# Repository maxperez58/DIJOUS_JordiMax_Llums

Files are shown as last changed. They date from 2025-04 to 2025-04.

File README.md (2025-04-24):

View this project on [CADLAB.io](https://cadlab.io/project/28977). 

DIJOUS_JordiMax_Llums

## Autors
- Max Pérez (@maxperez58)
- Jordi Godàs (@Jordi_Godas)

## Versió - v1.0 ## Curs - Assignatura de Disseny de PCBs amb KiCad - [Curs 2024-2025]

## Objectiu Descripció breu de l'objectiu del projecte.

L'objectiu d'aquest projecte és la realització d'un sistema de control per els diferents tipus de llums d'un vehícle automòvil. A més a més, s'ha incorporat un motor per al control de l'escombreta neteja-fars.

## Requisits i especificacions
- Llums curtes.
- Llums d'encreuament.
- Llums de circulacio dïurna.
- Intermitents.
- Motor escombreta neteja-fars.
- Sensor digital de llum, per activar les llums.

## Diagrama de blocs (Afegiu una imatge del diagrama de blocs)
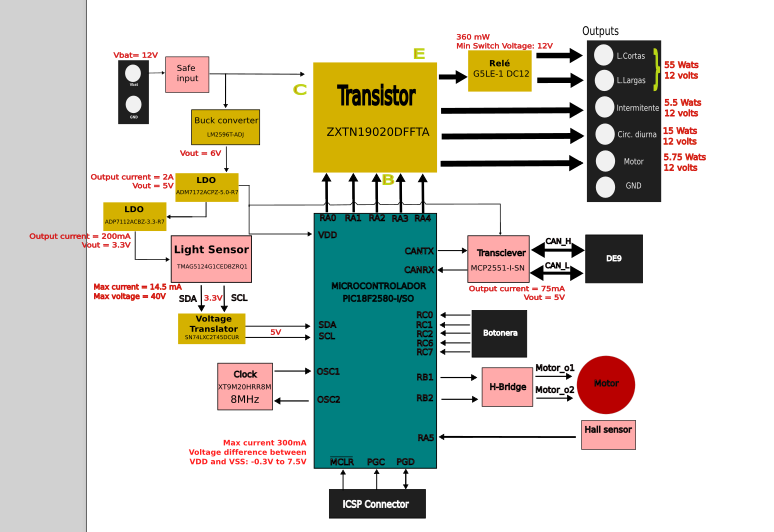
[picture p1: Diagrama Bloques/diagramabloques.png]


_Figura 1.1: Diagrama de Blocs del nostre projecte_

## Taula de components
| Descripció | Manufacturer Number | Package | Datasheet | Proveïdor | Unitats |
|---|---|---|---|---|---|
| LDO-5V | REG1117-5 |SMD| [LT1117-5](https://www.mouser.es/datasheet/2/609/1117fd-2953685.pdf)| Mouser | 1 |
| LDO-3.3V | ADP7112ACBZ-3.3-R7 |SMD| [ADP7112ACBZ-3.3-R7 ](https://www.mouser.es/datasheet/2/609/ADP7112-3121706.pdf)| Mouser | 1 |
| Sensor de llum | BH1750FVI-TR |SMD| [BH1750FVI-TR](https://www.mouser.com/catalog/specsheets/Rohm_11162017_ROHMS34826-1.pdf)| Mouser | 1 |
| Relé | G5LE-1 DC12 |TO-220| [G5LE-1 DC12](https://www.mouser.es/datasheet/2/307/en_g5le-3447037.pdf)| Mouser | 2 |
| Buck converter | LM2596T-ADJ |SMD| [LM2596T-ADJ](https://www.ti.com/lit/ds/symlink/lm2596.pdf)| Texas Instruments | 1 |
| Transciever| MCP2551-I-SN |SMD| [MCP2551-I-SN](https://ww1.microchip.com/downloads/en/devicedoc/21667d.pdf) | Texas Instruments | 1 |
| Microcontrolador | PIC18F2580-I/SO |SMD| [PIC18F2580-I/SO](https://www.mouser.es/datasheet/2/268/39637d-3443674.pdf) | Mouser | 1 |
| Transistor NMOS | Si7336ADP |SMD| [Si7336ADP](https://www.vishay.com/docs/73152/si7336adp.pdf)| Mouser | 4 |
| Transistor BJT | ZXTN19020DFFTA |SMD| [ZXTN19020DFFTA](https://www.diodes.com/assets/Datasheets/ZXTN19020DFF.pdf) | Mouser | 5 |
| Traductor (3.3V-5V) | PCA9306D |SMD|[PCA9306D](https://www.ti.com/lit/ds/symlink/pca9306.pdf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) | Mouser | 1 |
| Sensor hall | TMAG5124G1CEDBZRQ1 |SMD| [TMAG5124G1CEDBZRQ1](https://www.ti.com/lit/ds/symlink/tmag5124-q1.pdf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) | Mouser | 1 |
| OPAMP's | LT6202CS5 |SMD| [LT6202CS5](https://www.mouser.es/datasheet/2/609/620234fd-2955338.pdf) | Mouser | 1 |
| Voltage Regulator | TLV1117-33 |SMD| [TLV1117-33](http://www.ti.com/lit/ds/symlink/tlv1117.pdf) | Mouser | 1 |
| Cristall | XT9M20ANA8M |SMD| [XT9M20ANA8M](https://datasheet.octopart.com/XT9M20ANA8M-Vishay-datasheet-41303490.pdf) | Mouser | 1 |
| Inductance | Ms 42 / 47 µH |SMD| [Ms 42 / 47 µH](https://neosid.de/import-data/product-pdf/neoFestind_Ms42.pdf) | Mouser | 1 |
| Diode | 1N4002 |THT| [1N4002](https://diotec.com/request/datasheet/1n4001.pdf) | Mouser | 1 |
| Diode | 1N5817 |THT| [1N5817](http://www.vishay.com/docs/88525/1n5817.pdf) | Mouser | 4 |
| LED | APTR3216PGW |SMD| [APTR3216PGW](https://www.mouser.es/datasheet/2/216/kingbright_kngbd00006-5-1736195.pdf) | Mouser | 2 |
| Zener diode | BZX84C39 |SMD| [BZX84C39](https://diotec.com/request/datasheet/bzx84c2v4.pdf) | Mouser | 1 |
| Diode | 1N4148 |THT| [1N4148](https://assets.nexperia.com/documents/data-sheet/1N4148_1N4448.pdf) | Mouser | 1 |
| Diode Schottky | SS3P5HM3/84A |SMD| [SS3P5HM3/84A](https://www.vishay.com/docs/88944/ss3p3.pdf) | Mouser | 1 |

## Funcionalitats de les diverses seccions del nostre circuit
- [ ] Secció 1: secció de Power que converteix els 12 volts de VBAT a 5 volts per +Vcc i els 3.3 volts pel sensor.
- [ ] Secció 2: resistències pull-down a l'input per evitar una entrada descontrolada en cas de no connexió.
- [ ] Secció 3: secció del sensor amb traductor de nivell per garantir la bona comunicació entre sensor i microcontrolador.
- [ ] Secció 4: Etapa d'entrada del sensor Hall, el qual està destinat a comptar les voltes del motor.
- [ ] Secció 5: Etapa de comunicacions basada en un transciever el qual serveix per connectar el micro a un bus CAN.
- [ ] Secció 6: Etapa digital, formada pel micro i els seus I/0 + ICSP + Clock
- [ ] Secció 7: Pont-H + resistència Shunt, que controlen el sentit de gir del motor i detecten possibles pics de tensió
- [ ] Secció 8: etapa de selecció, on segons el corrent de base dels transistors i el voltatge aplicat al relé, s'escull un tipus d'iluminació o un altre.
- [ ] Secció 9: etapa reservada pels outputs i el connector DB-9 del bus CAN

## Historial de canvis 
| Data | Autor | Branch | Descripció |
|---|---|---|---|
| 2025-03-17 | Max Pérez | `main` | Creació del projecte |
| 2025-03-17 | Max Pérez | `main` | LDO y output select stage |
| 2025-03-18 | Max Pérez | `main` | Conexiones básicas micro|
| 2025-03-18 | Max Pérez | `main` |Bloque transceiver, safe input y Clock|
| 2025-03-18 | Max Pérez |  `main` |Mejora estética|
| 2025-03-19 | Jordi Godàs | `main`|Acabar el diagrama de blocs 1.0|
| 2025-03-19 | Jordi Godàs |  `main` |Acabar el power point de la presentació|
| 2025-03-21 | Max Pérez | `main` |Creación esquemático 1.0|
| 2025-03-21 | Max Pérez | `main` |Bloques Clock, Communication, Digital Esquemático 1.0|
| 2025-03-21 | Max Pérez |  `main` |Bloques Input, Sensor, Power Esquemático 1.0|
| 2025-03-22 | Max Pérez |  `main` |Mejora etapa Power cambiando DC/DC + LDO por Buck|
| 2025-03-21 | Max Pérez | `main` |Capacidades desacoplo, comentar esquemático y bloque output|
| 2025-03-24 | Max Pérez |  `main` |Simulación Power stage (1 buck y 2 LDO). Exitosa|
| 2025-03-25 | Max Pérez |  `main` |Simulación Power stage (1 buck y 2 LDO) v2 y simulación Puente H|
| 2025-03-27 | Jordi Godàs |  `main` | Actualizar presentacion |
| 2025-03-27 | Jordi Godàs |  `main` | Actualizar el diagrama de bloques y el esquematico con lo dicho en clase por el profesor |
| 2025-03-29 | Max Pérez |  `main` |simulación Puente H v2|
| 2025-03-31 | Max Pérez |  `main` |Placement algunos componentes, separación planos masa y potencia. Routing Transciever, puente H y algun Input Output|
| 2025-04-02 | Jordi Godàs |  `main` | Acabar el layout de la pcb |
| 2025-04-02 | Jordi Godàs |  `main` | Actualizar presentacion |
| 2025-04-02 | Max Pérez |  `main` |GND de SMD + algun ruteo puntual. DRC sin errores|
| 2025-04-03 | Jordi Godàs |  `main` | Cambio del LDO-3.3V y placement en el esquematico |
| 2025-04-03 | Jordi Godàs |  `main` | Update readme |
| 2025-04-06 | Jordi Godàs |  `main` | Update pcb, bigger paths and better organitzation |
| 2025-04-06 | Jordi Godàs |  `main` | Update schemetatic, minor changes |
| 2025-04-07 | Jordi Godàs |  `main` | Finished layout, ERC passed |
| 2025-04-12 | Max Pérez |  `main` | Update readme: update componentes usados + diagrama bloques i funcionalidades secciones|
| 2025-04-07 | Max Pérez |  `main` | Update Esquemàtic: nombrar nodos + corrección conexión etapa Shut|
| 2025-04-09 | Jordi Godàs |  `main` | Update layout: 2CI ERC passed |
| 2025-04-12 | Max Pérez |  `main` | Cambio LDO a 5V dado a la footprint conflictiva del anterior |
| 2025-04-12 | Max Pérez |  `main` | Revisión y sustitución de footprints mal asignadas, así como reorganización en el layout de la etapa de potencia |
| 2025-04-20 | Max Pérez |  `main` | Matriu de preus per a tirada curta PCBs|
| 2025-04-20 | Max Pérez |  `main` | Generació Gerbers|
| 2025-04-20 | Max Pérez |  `main` | Búsqueda precios JCL PCB y referencias en su catálogo|
| 2025-04-23 | Jordi Godàs |  `main` | Tirada curta dels presupostos |

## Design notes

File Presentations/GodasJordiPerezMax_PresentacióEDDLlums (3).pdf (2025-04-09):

# Projecte EDD-Llums

## Max Pérez Piqué Jordi Godàs Mancha

## Eines de Disseny

2024/2025

# Diagrama de blocs

# De què tracta el projecte?

Disseny del sistema de control d'il·luminació d’un cotxe mitjançant un microcontrolador.

# Requisits del projecte

## Parts clau del diagrama:

- Llums de carretera.
- Llums d'encreuament.
- Llums de circulació diürna.

## - Intermitents

- Motor escombreta neteja-fars.
- Sensor digital de llum, per activar les llums.

# Diagrama de blocs

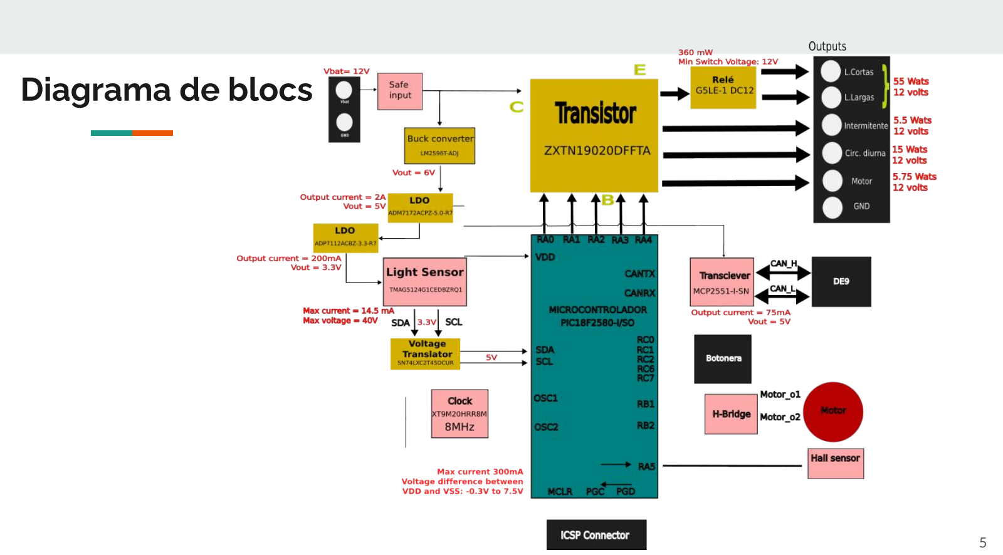
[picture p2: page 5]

# Inputs

# Output selection stage

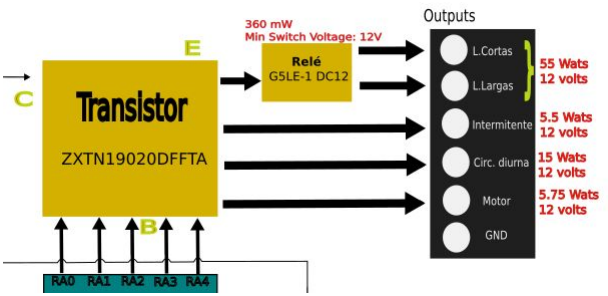
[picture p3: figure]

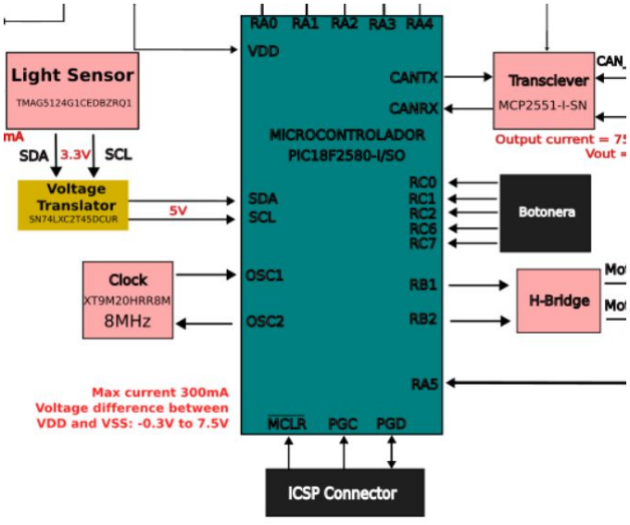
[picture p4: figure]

# Microcontrolador

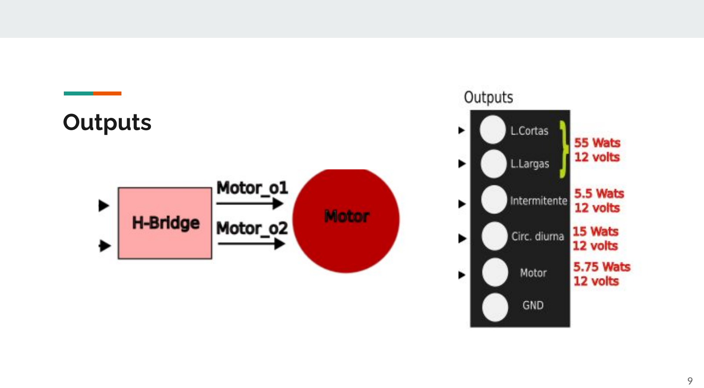
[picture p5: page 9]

# Outputs

# Esquemàtic

# Inputs

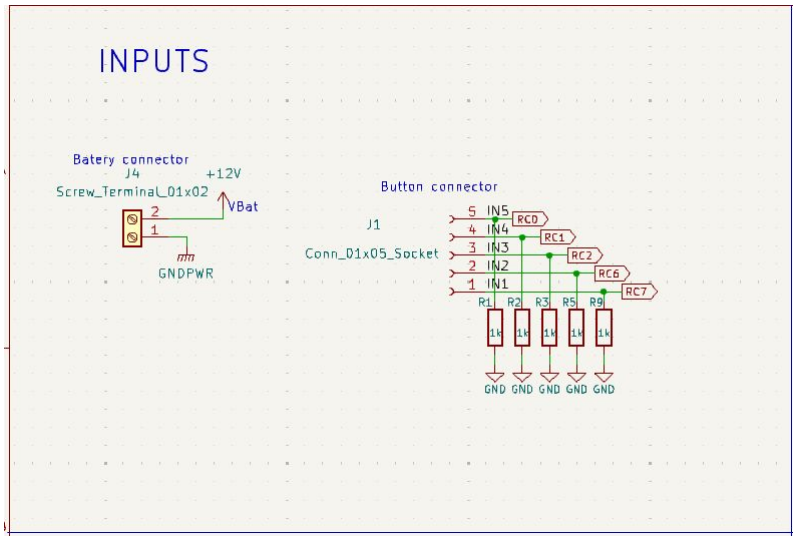
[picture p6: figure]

# Power

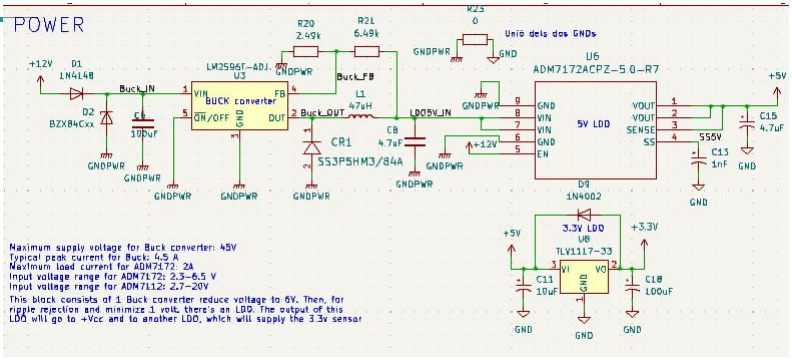
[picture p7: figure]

# Light Sensor

# Sensor Hall

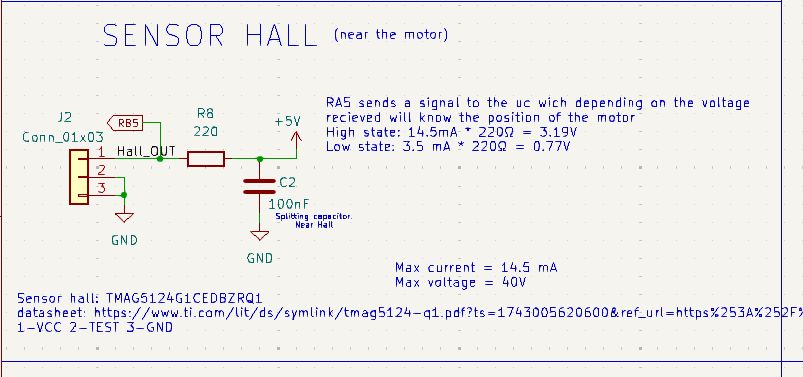
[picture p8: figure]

# Transceiver i leds

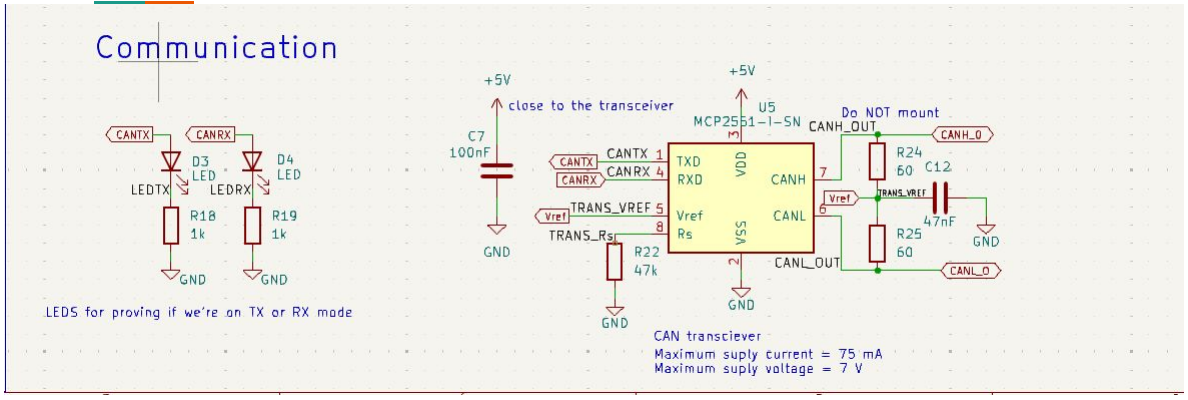
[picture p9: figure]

# H-bridge

# Output select stage

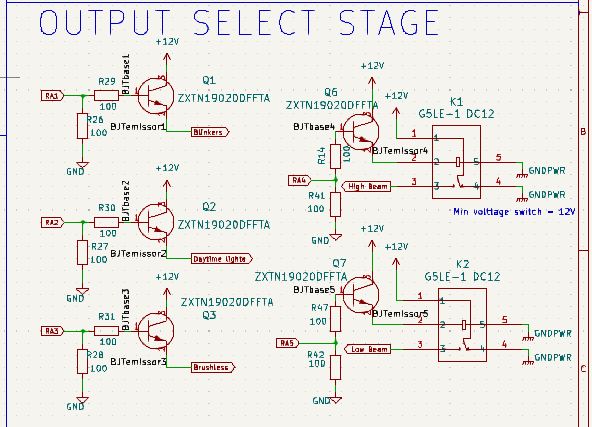
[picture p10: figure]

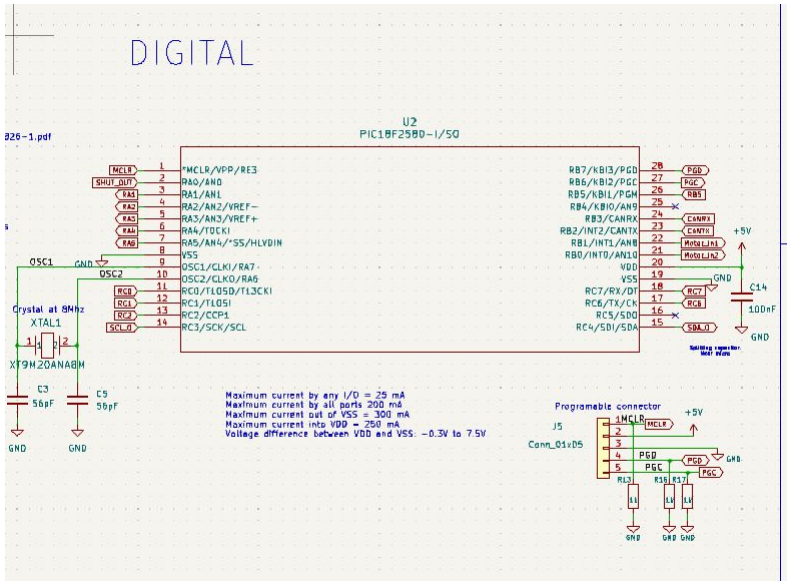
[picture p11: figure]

# Microcontrolador

# Outputs

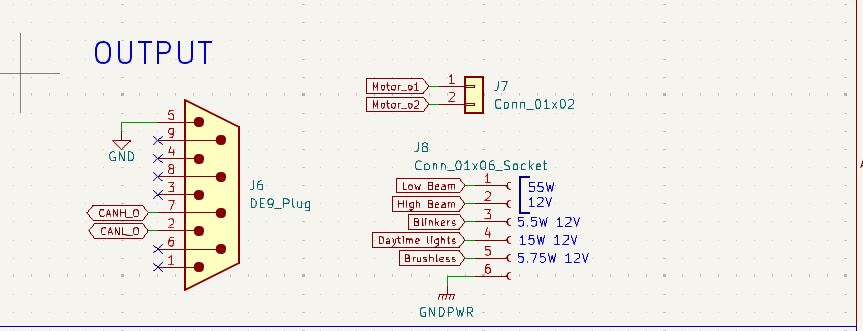
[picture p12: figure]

# Simulacions

# Power stage

## Etapa de potència

## Ripple LM2596:

# Power stage

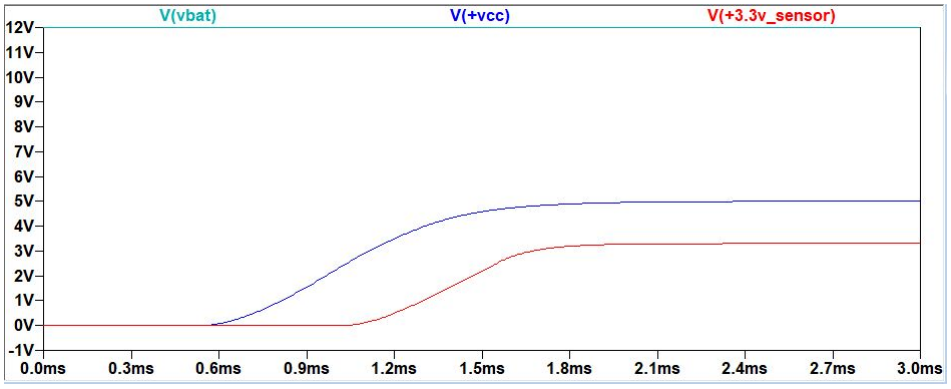
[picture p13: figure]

## Representació gràfica dels diferents voltatges de l’etapa de potència en funció del temps

# H-Bridge

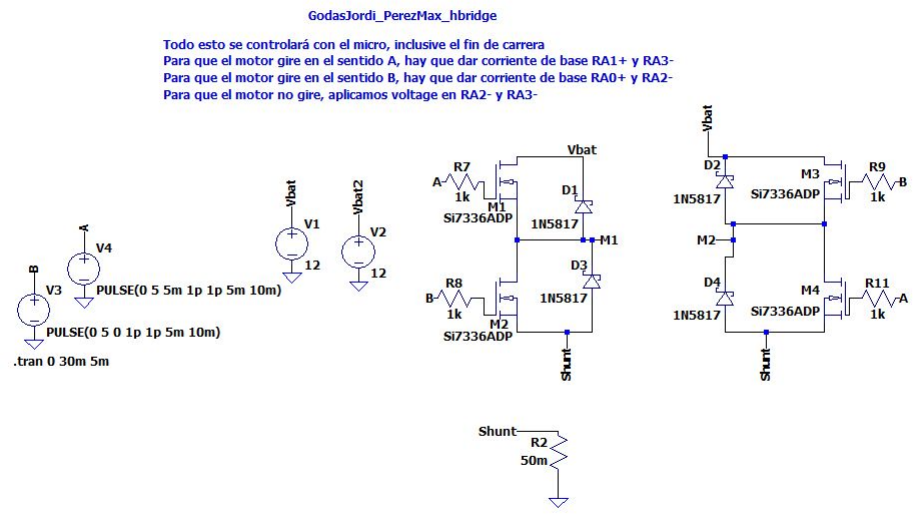
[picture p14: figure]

## Pont H per controlar el sentit de gir del motor i final de carrera

# H-Bridge

## Representació gràfica dels voltatges en el Pont H i corrent resistència Shunt

# Layout

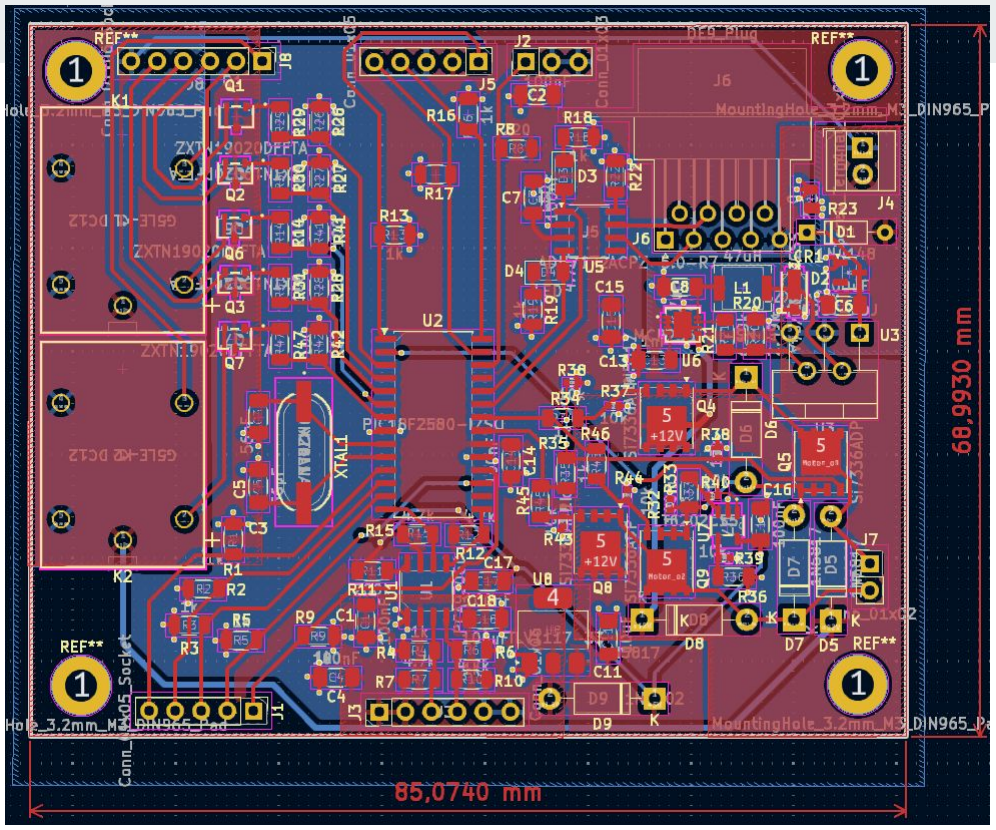
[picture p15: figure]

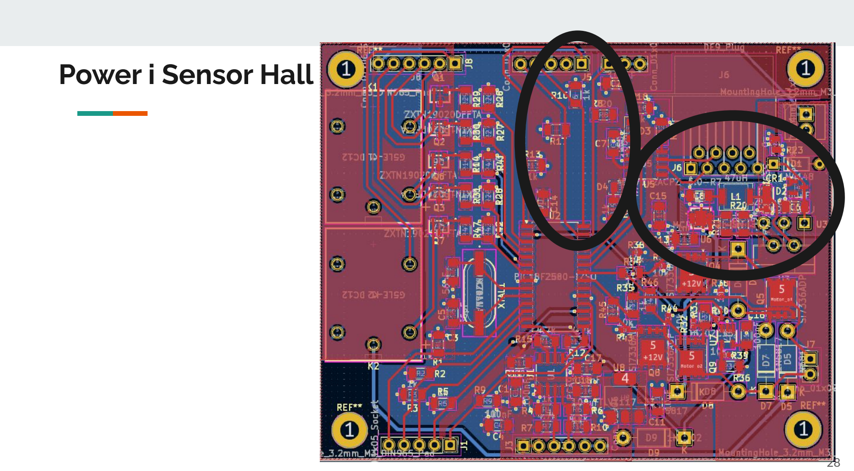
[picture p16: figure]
Power i Sensor Hall

# Power i Sensor Hall

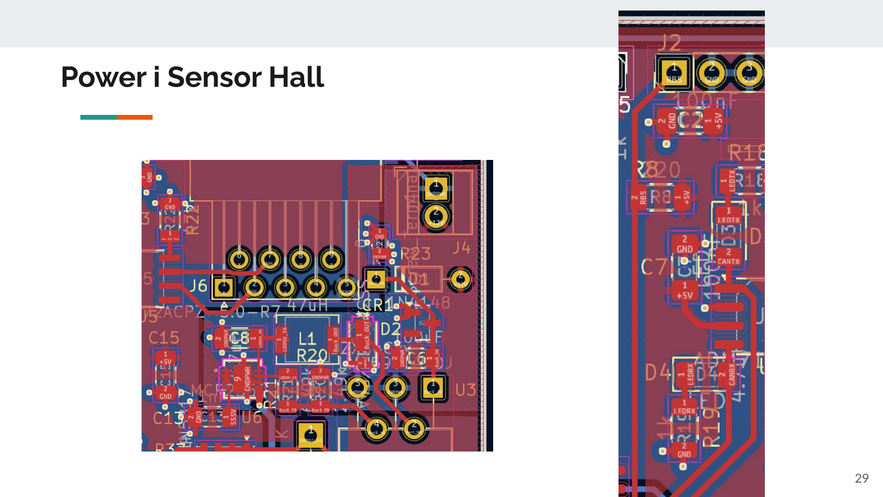
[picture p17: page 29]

# Light Sensor

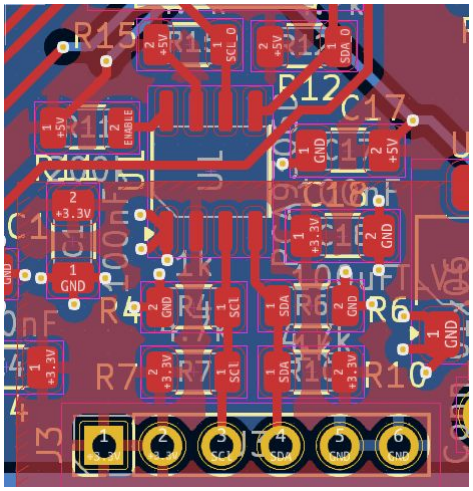
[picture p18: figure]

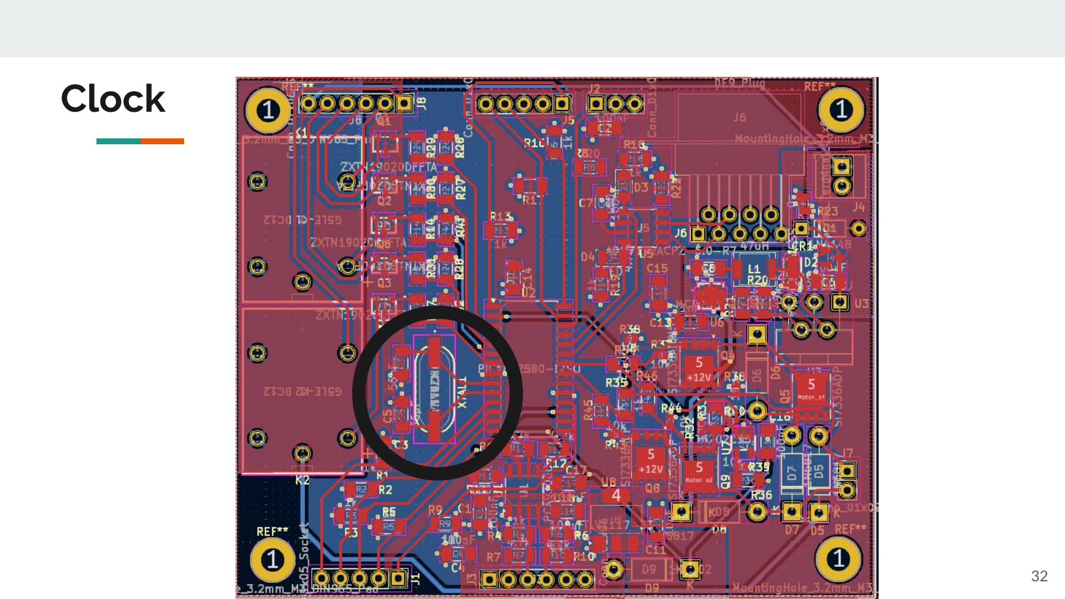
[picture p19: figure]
Clock

# Clock

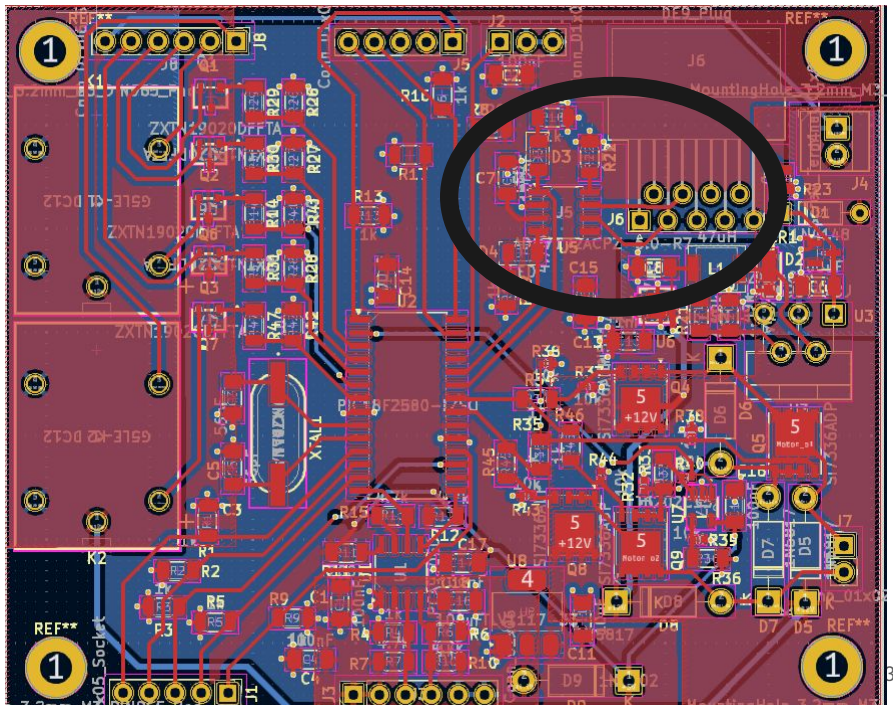
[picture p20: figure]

# Transceiver i leds

# Transceiver i leds

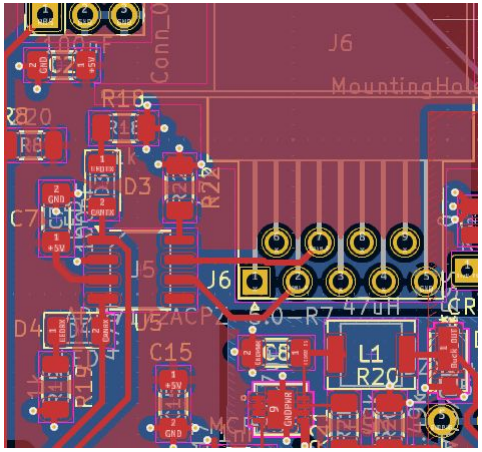
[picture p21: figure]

# H-bridge

# H-bridge

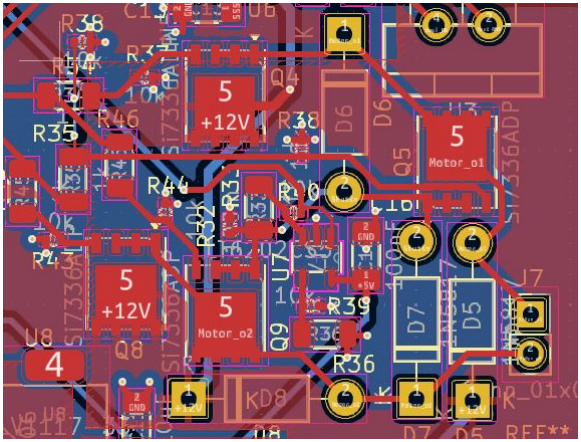
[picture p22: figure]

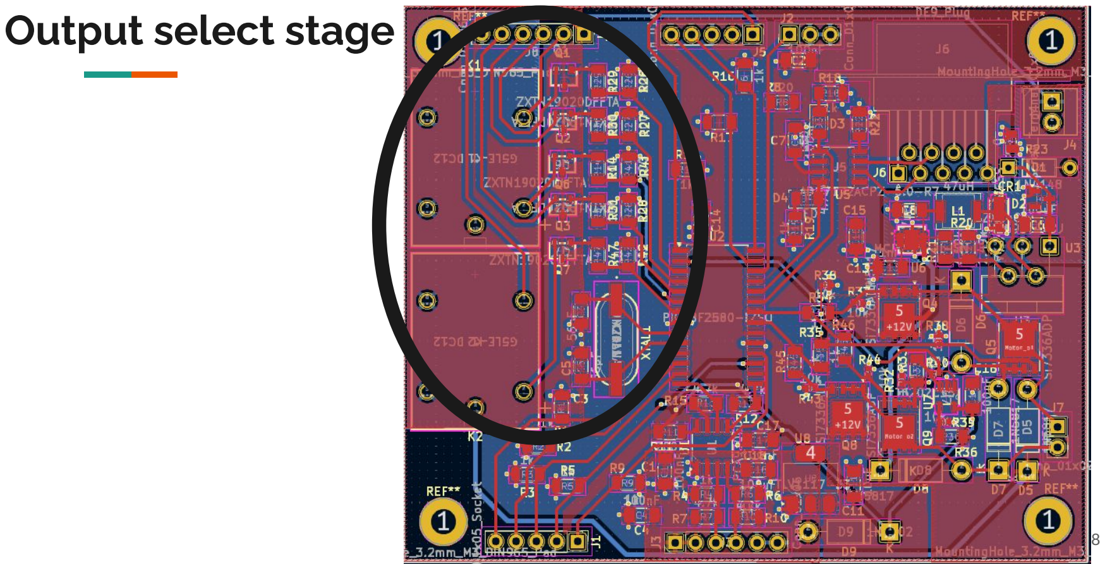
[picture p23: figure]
Output select stage

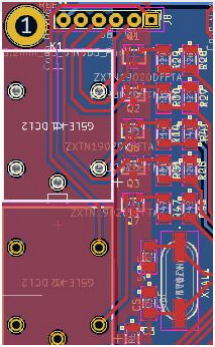
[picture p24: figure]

# Output select stage

# Microcontrolador

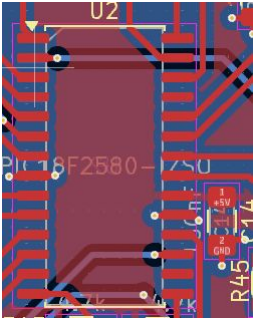
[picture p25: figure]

# Components

Nom del component | Funció | Datasheet
ADM7172ACPZ-5.0-R7 | LDO 5V | ADM7172ACPZ-5.0-R7 (https://www.mouser.es/datasheet/2/609/ADM7172-3121160.pdf)
ADP7112ACBZ-3.3-R7 | LDO 3.3V | ADP7112ACBZ-3.3-R7 (https://www.mouser.es/datasheet/2/609/ADP7112-3121706.pdf)
BH1750FVI-TR | Sensor de llum | BH1750FVI-TR (https://www.mouser.com/catalog/specsheets/Rohm_11162017_ROHMS34826-1.pdf)
G5LE-1 DC12 | Relé | G5LE-1 DC12 (https://www.mouser.es/datasheet/2/307/en_g5le-3447037.pdf)
LM2596T-ADJ | BUCK converter | LM2596T-ADJ (http://www.ti.com/lit/ds/symlink/lm2596.pdf)
MCP2551-I-SN | Transciever | MCP2551-I-SN (http://ww1.microchip.com/downloads/en/devicedoc/21667d.pdf)
PIC18F2580-I/SO | Microprocesador | PIC18F2580-I/SO (https://ww1.microchip.com/downloads/aemDocuments/documents/OTH/ProductDocuments/DataSheets/39637d.pdf)
Si7336ADP | Transistor BJT | Si7336ADP (https://www.vishay.com/docs/73152/si7336adp.pdf)
SN74LXC2T45DCUR | Traductor de 5V a 3.3V | SN74LXC2T45DCUR (https://www.ti.com/lit/ds/symlink/sn74lxc2t45.pdf?ts=1742941073769)
TMAG5124G1CEDBZRQ1 | Sensor hall | TMAG5124G1CEDBZRQ1 (https://www.ti.com/lit/ds/symlink/tmag5124-q1.pdf?ts=1743005620600)
ZXTN19020DFFTA | Transistor mosfet | ZXTN19020DFFTA (https://www.diodes.com/assets/Datasheets/ZXTN19020DFF.pdf)
PCA9306D | Tracuctor de nivells | PCA9036 (https://www.ti.com/lit/ds/symlink/pca9306.pdf?ts=1743021004009)
XT9M20HRR8M | Cristall | XT9M20HRR8M (https://datasheet.octopart.com/XT9M20ANA8M-Vishay-datasheet-41303490.pdf)

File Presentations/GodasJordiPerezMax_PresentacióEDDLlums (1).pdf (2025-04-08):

# Projecte EDD-Llums

## Max Pérez Piqué Jordi Godàs Mancha

## Eines de Disseny

2024/2025

# Diagrama de blocs

# De què tracta el projecte?

Disseny del sistema de control d'il·luminació d’un cotxe mitjançant un microcontrolador.

# Requisits del projecte

## Parts clau del diagrama:

- Llums de carretera.
- Llums d'encreuament.
- Llums de circulació diürna.

## - Intermitents

- Motor escombreta neteja-fars.
- Sensor digital de llum, per activar les llums.

# Diagrama de blocs


# Inputs

# Output selection stage



# Microcontrolador

# Outputs

# Esquemàtic


# Inputs


# Power

# Light Sensor


# Sensor Hall i Clock


# Transceiver i leds


# H-bridge

# Output select stage


# Microcontrolador


# Outputs

# Simulacions

# Power stage


## Etapa de potència

## Ripple LM2596:

# Power stage


## Representació gràfica dels diferents voltatges de l’etapa de potència en funció del temps

# H-Bridge

## Pont H per controlar el sentit de gir del motor i final de carrera

# H-Bridge


## Representació gràfica dels voltatges en el Pont H i corrent resistència Shunt

# Layout



# Power i Sensor Hall


# Light Sensor

Clock

# Clock


# Transceiver i leds

# Transceiver i leds


# H-bridge


# H-bridge

H-bridge


# Output select stage


# Microcontrolador

# Components

Nom del component | Funció | Datasheet
ADM7172ACPZ-5.0-R7 | LDO 5V | ADM7172ACPZ-5.0-R7 (https://www.mouser.es/datasheet/2/609/ADM7172-3121160.pdf)
ADP7112ACBZ-3.3-R7 | LDO 3.3V | ADP7112ACBZ-3.3-R7 (https://www.mouser.es/datasheet/2/609/ADP7112-3121706.pdf)
BH1750FVI-TR | Sensor de llum | BH1750FVI-TR (https://www.mouser.com/catalog/specsheets/Rohm_11162017_ROHMS34826-1.pdf)
G5LE-1 DC12 | Relé | G5LE-1 DC12 (https://www.mouser.es/datasheet/2/307/en_g5le-3447037.pdf)
LM2596T-ADJ | BUCK converter | LM2596T-ADJ (http://www.ti.com/lit/ds/symlink/lm2596.pdf)
MCP2551-I-SN | Transciever | MCP2551-I-SN (http://ww1.microchip.com/downloads/en/devicedoc/21667d.pdf)
PIC18F2580-I/SO | Microprocesador | PIC18F2580-I/SO (https://ww1.microchip.com/downloads/aemDocuments/documents/OTH/ProductDocuments/DataSheets/39637d.pdf)
Si7336ADP | Transistor BJT | Si7336ADP (https://www.vishay.com/docs/73152/si7336adp.pdf)
SN74LXC2T45DCUR | Traductor de 5V a 3.3V | SN74LXC2T45DCUR (https://www.ti.com/lit/ds/symlink/sn74lxc2t45.pdf?ts=1742941073769)
TMAG5124G1CEDBZRQ1 | Sensor hall | TMAG5124G1CEDBZRQ1 (https://www.ti.com/lit/ds/symlink/tmag5124-q1.pdf?ts=1743005620600)
ZXTN19020DFFTA | Transistor mosfet | ZXTN19020DFFTA (https://www.diodes.com/assets/Datasheets/ZXTN19020DFF.pdf)
PCA9036 | Tracuctor de nivells | PCA9036 (https://www.ti.com/lit/ds/symlink/pca9306.pdf?ts=1743021004009)
XT9M20HRR8M | Cristall | XT9M20HRR8M (https://datasheet.octopart.com/XT9M20ANA8M-Vishay-datasheet-41303490.pdf)

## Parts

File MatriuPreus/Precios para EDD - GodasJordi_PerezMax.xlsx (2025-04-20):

 | Tirada curta (10 PCBs) |  |  |  |  |  |  |  |  |  |  | Tirada llarga (1.000 PCBs)
Info | Components | Producte | Unitats | Preu/unitat | Preu | Distribuidor | Disponibilitat |  |  |  | Info | Components | Producte | Unitats | Preu/unitat | Preu | Distribuidor | Disponibilitat
 |  | REG1117-5 | 1 | 2.14 | 21.4 | Mouser | Inmediat |  |  |  |  |  | REG1117-5 | 1 |  | 0 | Mouser
 |  | ADP7112ACBZ-3.3-R7 | 1 | 1.25 | 12.5 | Mouser | Inmediat |  |  |  |  |  | ADP7112ACBZ-3.3-R7 | 1 |  | 0 | Mouser
 |  | BH1750FVI-TR | 1 | 2.42 | 24.2 | Mouser | Inmediat |  |  |  |  |  | BH1750FVI-TR | 1 |  | 0 | Mouser
 |  | G5LE-1 DC12 | 2 | 1.32 | 26.4 | Mouser | Inmediat |  |  |  |  |  | G5LE-1 DC12 | 2 |  | 0 | Mouser
 |  | LM2596T-ADJ | 1 | 4.03 | 35.47609 | DigiKey | Inmediat |  |  |  |  |  | LM2596T-ADJ | 1 |  | 0 | DigiKey
 |  | MCP2551-I-SN | 1 | 1.29 | 12.9 | Mouser | Inmediat |  |  |  |  |  | MCP2551-I-SN | 1 |  | 0 | Mouser
 |  | PIC18F2580-I/SO | 1 | 7.72 | 77.2 | Mouser | Inmediat |  |  |  |  |  | PIC18F2580-I/SO | 1 |  | 0 | Mouser
 |  | Si7336ADP | 4 | 1.3 | 52 | Mouser | Inmediat |  |  |  |  |  | Si7336ADP | 4 |  | 0 | Mouser
 |  | ZXTN19020DFFTA | 5 | 0.678 | 33.9 | Mouser | Inmediat |  |  |  |  |  | ZXTN19020DFFTA | 5 |  | 0 | Mouser
 |  | PCA9306D | 1 | 0.402 | 4.02 | Mouser | Inmediat |  |  |  |  |  | PCA9306D | 1 |  | 0 | Mouser
 |  | TMAG5124G1CEDBZRQ1 | 1 | 0.653 | 6.53 | Mouser | Inmediat |  |  |  |  |  | TMAG5124G1CEDBZRQ1 | 1 |  | 0 | Mouser
 |  | LT6202CS5 | 1 | 3.61 | 36.1 | Mouser | Inmediat |  |  |  |  |  | LT6202CS5 | 1 |  | 0 | Mouser
 |  | TLV1117-33 | 1 | 0.511 | 5.11 | Mouser | Inmediat |  |  |  |  |  | TLV1117-33 | 1 |  | 0 | Mouser
 |  | XT9M20ANA8M | 1 | 0.508 | 5.08 | Mouser | Inmediat |  |  |  |  |  | XT9M20ANA8M | 1 |  | 0 | Mouser
 |  | CBC3225T470MRV | 1 | 0.156 | 1.56 | Mouser | Inmediat | Preu/placa |  |  |  |  | CBC3225T470MRV | 1 |  | 0 | Mouser
 |  | 1N4002 | 1 | 0.069 | 0.69 | Mouser | Inmediat | Tirada curta | 10 plaques | 72.5109865 |  |  | 1N4002 | 1 |  | 0 | Mouser
 |  | 1N5817 | 4 | 0.157 | 6.28 | Mouser | Inmediat |  | 50 plaques | 60.71236877 |  |  | 1N5817 | 4 |  | 0 | Mouser
 |  | APTR3216PGW | 2 | 0.291 | 5.82 | Mouser | Inmediat | Tirada llarga | 1000 plaques |  |  |  | APTR3216PGW | 2 |  | 0 | Mouser
 |  | BZX84C39 | 1 | 0.09 | 0.9 | Mouser | Inmediat |  | 10k plaques |  |  |  | BZX84C39 | 1 |  | 0 | Mouser
 |  | 1N4148 | 1 | 0.037 | 0.37 | Mouser | Inmediat |  |  |  |  |  | 1N4148 | 1 |  | 0 | Mouser
 |  | SS3P5HM3/84A | 1 | 0.136 | 1.36 | Mouser | Inmediat |  |  |  |  |  | SS3P5HM3/84A | 1 |  | 0 | Mouser
(Cap 100nF) |  | C1206C164K5GLCAUTO | 7 | 2.21 | 154.7 | Mouser | Inmediat | Dollar a 19/4/25 |  |  | (Cap 100nF) |  | C1206C164K5GLCAUTO | 7 |  | 0 | Mouser
(Cap 56pF) |  | KGQ15ACG2A560FT | 2 | 0.205 | 4.1 | Mouser | Inmediat | 1 USD | 0.8803 | EUR | (Cap 56pF) |  | KGQ15ACG2A560FT | 2 |  | 0 | Mouser
(Cap 100uF) |  | TLCT107M010XTA | 2 | 3.27 | 65.4 | Mouser | Inmediat |  |  |  | (Cap 100uF) |  | TLCT107M010XTA | 2 |  | 0 | Mouser
(Cap 4.7uF) |  | CL05X475MQ5NRWC | 1 | 0.186 | 1.86 | Mouser | Inmediat |  |  |  | (Cap 4.7uF) |  | CL05X475MQ5NRWC | 1 |  | 0 | Mouser
(Cap 10u) |  | KGM03DS60E106MH | 1 | 0.496 | 4.96 | Mouser | Inmediat |  |  |  | (Cap 10u) |  | KGM03DS60E106MH | 1 |  | 0 | Mouser
(Cap 22u) |  | GRM188D70J226ME01D | 1 | 0.2 | 2 | Mouser | Inmediat |  |  |  | (Cap 22u) |  | GRM188D70J226ME01D | 1 |  | 0 | Mouser
(Cap 10uF) |  | KGM03DS60E106MH | 1 | 0.496 | 4.96 | Mouser | Inmediat |  |  |  | (Cap 10uF) |  | KGM03DS60E106MH | 1 |  | 0 | Mouser
Con 5 pin |  | PinHeader 1x05 2.54mm | 2 | 0.2359204 | 4.718408 | DigiKey | Inmediat |  |  |  | Con 5 pin |  | PinHeader 1x05 2.54mm | 2 |  | 0 | DigiKey
Con 3 pin |  | PinHeader 1x03 2.54mm | 1 | 0.0325711 | 0.325711 | DigiKey | Inmediat |  |  |  | Con 3 pin |  | PinHeader 1x03 2.54mm | 1 |  | 0 | DigiKey
Conn 6 pin |  | PinHeader 1x06 2.54mm | 2 | 0.2359204 | 4.718408 | DigiKey | Inmediat |  |  |  | Conn 6 pin |  | PinHeader 1x06 2.54mm | 2 |  | 0 | DigiKey
Screw 2 pin |  | EBWA-02-B | 1 | 0.325711 | 3.25711 | DigiKey | Inmediat |  |  |  | Screw 2 pin |  | EBWA-02-B | 1 |  | 0 | DigiKey
DB9 |  | 618009231221 | 1 | 2.1470517 | 21.470517 | DigiKey | Inmediat |  |  |  | DB9 |  | 618009231221 | 1 |  | 0 | DigiKey
 |  | 61300211121 | 1 | 0.0897906 | 0.897906 | DigiKey | Inmediat |  |  |  |  |  | 61300211121 | 1 |  | 0 | DigiKey
R 1k |  | RCV12063M00JNEA | 18 | 0.116 | 20.88 | Mouser | Inmediat |  |  |  | R 1k |  | RCV12063M00JNEA | 18 |  | 0 | Mouser
R 4.7k |  | RC1206FR-134K7L | 4 | 0.0167257 | 0.669028 | DigiKey | Inmediat |  |  |  | R 4.7k |  | RC1206FR-134K7L | 4 |  | 0 | DigiKey
R 220 |  | RC1206FR-10220RL | 1 | 0.0167257 | 0.167257 | DigiKey | Inmediat |  |  |  | R 220 |  | RC1206FR-10220RL | 1 |  | 0 | DigiKey
R 200k |  | RC1206FR-07200KL | 1 | 0.0158454 | 0.158454 | Digikey | Inmediat |  |  |  | R 200k |  | RC1206FR-07200KL | 1 |  | 0 | Digikey
R 100 |  | RC1206FR-10100RL | 10 | 0.01522919 | 1.522919 | Digikey | Inmediat |  |  |  | R 100 |  | RC1206FR-10100RL | 10 |  | 0 | Digikey
R 2k |  | RC1206DR-072KL | 1 | 0.0598604 | 0.598604 | DigiKey | Inmediat |  |  |  | R 2k |  | RC1206DR-072KL | 1 |  | 0 | DigiKey
R 6.81k |  | D55342K07B6E81RWB | 1 | 1.29 | 12.9 | Mouser | Inmediat |  |  |  | R 6.81k |  | D55342K07B6E81RWB | 1 |  | 0 | Mouser
R 47k |  | CRT1206-FX-4702ELF | 1 | 0.248 | 2.48 | Mouser | Inmediat |  |  |  | R 47k |  | CRT1206-FX-4702ELF | 1 |  | 0 | Mouser
R 100m |  | ERJ-8RSFR10V | 1 | 0.171 | 1.71 | Mouser | Inmediat |  |  |  | R 100m |  | ERJ-8RSFR10V | 1 |  | 0 | Mouser
R 10k |  | RNCE1206BTE10K0 | 6 | 0.16 | 9.6 | Mouser | Inmediat |  |  |  | R 10k |  | RNCE1206BTE10K0 | 6 |  | 0 | Mouser
 | PCB | PCB | N/A | 12.2 | 10.73966 | JLCPCB | 24 hours |  |  |  |  | PCB | PCB | N/A |  | 0 | JLC PCB
Gratis per +50euros | Shipping | PCB | N/A | 23.31 | 20.519793 | JLCPCB | 24 hours |  |  |  | Gratis per +50euros | Shipping | PCB | N/A |  | 0 | JLC PCB
Gratis +50 euros |  | Mouser | N/A | 0 | 0 | Mouser | Inmediat |  |  |  | Gratis +50 euros |  | Mouser | N/A |  | 0 | Mouser
 |  | Digikey | N/A | 0 | 0 | DigiKey | Inmediat |  |  |  |  |  | Digikey | N/A |  | 0 | DigiKey
 | Total |  |  |  | 725.109865 |  |  |  |  |  |  | Total |  |  |  | 0
 | Tirada curta (50 PCBs) |  |  |  |  |  |  |  |  |  |  | Tirada llarga (20.000 PCBs)
Info | Components | Producte | Unitats | Preu/unitat | Preu | Distribuidor | Disponibilitat |  |  |  | Info | Components | Producte | Unitats | Preu/unitat | Preu | Distribuidor | Disponibilitat
 |  | REG1117-5 | 1 | 1.95 | 97.5 | Mouser | Inmediat |  |  |  |  |  | REG1117-5 | 1 |  | 0 | Mouser
 |  | ADP7112ACBZ-3.3-R7 | 1 | 1.14 | 57 | Mouser | Inmediat |  |  |  |  |  | ADP7112ACBZ-3.3-R7 | 1 |  | 0 | Mouser
 |  | BH1750FVI-TR | 1 | 2.42 | 121 | Mouser | Inmediat |  |  |  |  |  | BH1750FVI-TR | 1 |  | 0 | Mouser
 |  | G5LE-1 DC12 | 2 | 1.07 | 107 | Mouser | Inmediat |  |  |  |  |  | G5LE-1 DC12 | 2 |  | 0 | Mouser
 |  | LM2596T-ADJ | 1 | 4.90156 | 215.7421634 | DigiKey | Inmediat |  |  |  |  |  | LM2596T-ADJ | 1 |  | 0 | DigiKey
 |  | MCP2551-I-SN | 1 | 1.1 | 55 | Mouser | Inmediat |  |  |  |  |  | MCP2551-I-SN | 1 |  | 0 | Mouser
 |  | PIC18F2580-I/SO | 1 | 7.72 | 386 | Mouser | Inmediat |  |  |  |  |  | PIC18F2580-I/SO | 1 |  | 0 | Mouser
 |  | Si7336ADP | 4 | 1.25 | 250 | Mouser | Inmediat |  |  |  |  |  | Si7336ADP | 4 |  | 0 | Mouser
 |  | ZXTN19020DFFTA | 5 | 0.46 | 115 | Mouser | Inmediat |  |  |  |  |  | ZXTN19020DFFTA | 5 |  | 0 | Mouser
 |  | PCA9306D | 1 | 0.365 | 18.25 | Mouser | Inmediat |  |  |  |  |  | PCA9306D | 1 |  | 0 | Mouser
 |  | TMAG5124G1CEDBZRQ1 | 1 | 0.653 | 32.65 | Mouser | Inmediat |  |  |  |  |  | TMAG5124G1CEDBZRQ1 | 1 |  | 0 | Mouser
 |  | LT6202CS5 | 1 | 3.33 | 166.5 | Mouser | Inmediat |  |  |  |  |  | LT6202CS5 | 1 |  | 0 | Mouser
 |  | TLV1117-33 | 1 | 0.46 | 23 | Mouser | Inmediat |  |  |  |  |  | TLV1117-33 | 1 |  | 0 | Mouser
 |  | XT9M20ANA8M | 1 | 0.489 | 24.45 | Mouser | Inmediat |  |  |  |  |  | XT9M20ANA8M | 1 |  | 0 | Mouser
 |  | CBC3225T470MRV | 1 | 0.156 | 7.8 | Mouser | Inmediat |  |  |  |  |  | CBC3225T470MRV | 1 |  | 0 | Mouser
 |  | 1N4002 | 1 | 0.069 | 3.45 | Mouser | Inmediat |  |  |  |  |  | 1N4002 | 1 |  | 0 | Mouser
 |  | 1N5817 | 4 | 0.115 | 23 | Mouser | Inmediat |  |  |  |  |  | 1N5817 | 4 |  | 0 | Mouser
 |  | APTR3216PGW | 2 | 0.13 | 13 | Mouser | Inmediat |  |  |  |  |  | APTR3216PGW | 2 |  | 0 | Mouser
 |  | BZX84C39 | 1 | 0.09 | 4.5 | Mouser | Inmediat |  |  |  |  |  | BZX84C39 | 1 |  | 0 | Mouser
 |  | 1N4148 | 1 | 0.037 | 1.85 | Mouser | Inmediat |  |  |  |  |  | 1N4148 | 1 |  | 0 | Mouser
 |  | SS3P5HM3/84A | 1 | 0.136 | 6.8 | Mouser | Inmediat |  |  |  |  |  | SS3P5HM3/84A | 1 |  | 0 | Mouser
(Cap 100nF) |  | C1206C164K5GLCAUTO | 7 | 1.7 | 595 | Mouser | Inmediat |  |  |  | (Cap 100nF) |  | C1206C164K5GLCAUTO | 7 |  | 0 | Mouser
(Cap 56pF) |  | KGQ15ACG2A560FT | 2 | 0.13 | 13 | Mouser | Inmediat |  |  |  | (Cap 56pF) |  | KGQ15ACG2A560FT | 2 |  | 0 | Mouser
(Cap 100uF) |  | TLCT107M010XTA | 2 | 2.47 | 247 | Mouser | Inmediat |  |  |  | (Cap 100uF) |  | TLCT107M010XTA | 2 |  | 0 | Mouser
(Cap 4.7uF) |  | CL05X475MQ5NRWC | 1 | 0.186 | 9.3 | Mouser | Inmediat |  |  |  | (Cap 4.7uF) |  | CL05X475MQ5NRWC | 1 |  | 0 | Mouser
(Cap 10u) |  | KGM03DS60E106MH | 1 | 0.496 | 24.8 | Mouser | Inmediat |  |  |  | (Cap 10u) |  | KGM03DS60E106MH | 1 |  | 0 | Mouser
(Cap 22u) |  | GRM188D70J226ME01D | 1 | 0.2 | 10 | Mouser | Inmediat |  |  |  | (Cap 22u) |  | GRM188D70J226ME01D | 1 |  | 0 | Mouser
(Cap 10uF) |  | KGM03DS60E106MH | 1 | 0.496 | 24.8 | Mouser | Inmediat |  |  |  | (Cap 10uF) |  | KGM03DS60E106MH | 1 |  | 0 | Mouser
Con 5 pin |  | PinHeader 1x05 2.54mm | 2 | 0.1171 | 11.71 | DigiKey | Inmediat |  |  |  | Con 5 pin |  | PinHeader 1x05 2.54mm | 2 |  | 0 | DigiKey
Con 3 pin |  | PinHeader 1x03 2.54mm | 1 | 0.0656 | 3.28 | DigiKey | Inmediat |  |  |  | Con 3 pin |  | PinHeader 1x03 2.54mm | 1 |  | 0 | DigiKey
Conn 6 pin |  | PinHeader 1x06 2.54mm | 2 | 0.1552 | 15.52 | DigiKey | Inmediat |  |  |  | Conn 6 pin |  | PinHeader 1x06 2.54mm | 2 |  | 0 | DigiKey
Screw 2 pin |  | EBWA-02-B | 1 | 0.268 | 13.4 | DigiKey | Inmediat |  |  |  | Screw 2 pin |  | EBWA-02-B | 1 |  | 0 | DigiKey
DB9 |  | 618009231221 | 1 | 2.0006 | 100.03 | DigiKey | Inmediat |  |  |  | DB9 |  | 618009231221 | 1 |  | 0 | DigiKey
 |  | 61300211121 | 1 | 0.0656 | 3.28 | DigiKey | Inmediat |  |  |  |  |  | 61300211121 | 1 |  | 0 | DigiKey
R 1k |  | RCV12063M00JNEA | 18 | 0.049 | 44.1 | Mouser | Inmediat |  |  |  | R 1k |  | RCV12063M00JNEA | 18 |  | 0 | Mouser
R 4.7k |  | RC1206FR-134K7L | 4 | 0.017 | 3.4 | DigiKey | Inmediat |  |  |  | R 4.7k |  | RC1206FR-134K7L | 4 |  | 0 | DigiKey
R 220 |  | RC1206FR-10220RL | 1 | 0.018 | 0.9 | DigiKey | Inmediat |  |  |  | R 220 |  | RC1206FR-10220RL | 1 |  | 0 | DigiKey
R 200k |  | RC1206FR-07200KL | 1 | 0.017 | 0.85 | Digikey | Inmediat |  |  |  | R 200k |  | RC1206FR-07200KL | 1 |  | 0 | Digikey
R 100 |  | RC1206FR-10100RL | 10 | 0.016 | 8 | Digikey | Inmediat |  |  |  | R 100 |  | RC1206FR-10100RL | 10 |  | 0 | Digikey
R 2k |  | RC1206DR-072KL | 1 | 0.063 | 3.15 | DigiKey | Inmediat |  |  |  | R 2k |  | RC1206DR-072KL | 1 |  | 0 | DigiKey
R 6.81k |  | D55342K07B6E81RWB | 1 | 1.29 | 64.5 | Mouser | Inmediat |  |  |  | R 6.81k |  | D55342K07B6E81RWB | 1 |  | 0 | Mouser
R 47k |  | CRT1206-FX-4702ELF | 1 | 0.194 | 9.7 | Mouser | Inmediat |  |  |  | R 47k |  | CRT1206-FX-4702ELF | 1 |  | 0 | Mouser
R 100m |  | ERJ-8RSFR10V | 1 | 0.141 | 7.05 | Mouser | Inmediat |  |  |  | R 100m |  | ERJ-8RSFR10V | 1 |  | 0 | Mouser
R 10k |  | RNCE1206BTE10K0 | 6 | 0.152 | 45.6 | Mouser | Inmediat |  |  |  | R 10k |  | RNCE1206BTE10K0 | 6 |  | 0 | Mouser
 | PCB | PCB | N/A | 20.6 | 18.13418 | JLC PCB | 24 hours |  |  |  |  | PCB | PCB | N/A |  | #VALUE! | JLC PCB
Gratis per +50euros | Shipping | PCB | N/A | 33.65 | 29.622095 | JLC PCB | 24 hours |  |  |  | Gratis per +50euros | Shipping | PCB | N/A |  | #VALUE! | JLC PCB
Gratis +50 euros |  | Mouser | N/A | 0 | 0 | Mouser | Inmediat |  |  |  | Gratis +50 euros |  | Mouser | N/A |  | #VALUE! | Mouser
 |  | Digikey | N/A | 0 | 0 | DigiKey | Inmediat |  |  |  |  |  | Digikey | N/A |  | #VALUE! | DigiKey
 | Total |  |  |  | 3035.618438 |  |  |  |  |  |  | Total |  |  |  | #VALUE!

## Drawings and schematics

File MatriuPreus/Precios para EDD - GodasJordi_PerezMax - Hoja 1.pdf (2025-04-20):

Tirada curta (10 PCBs) | Tirada llarga (1.000 PCBs)

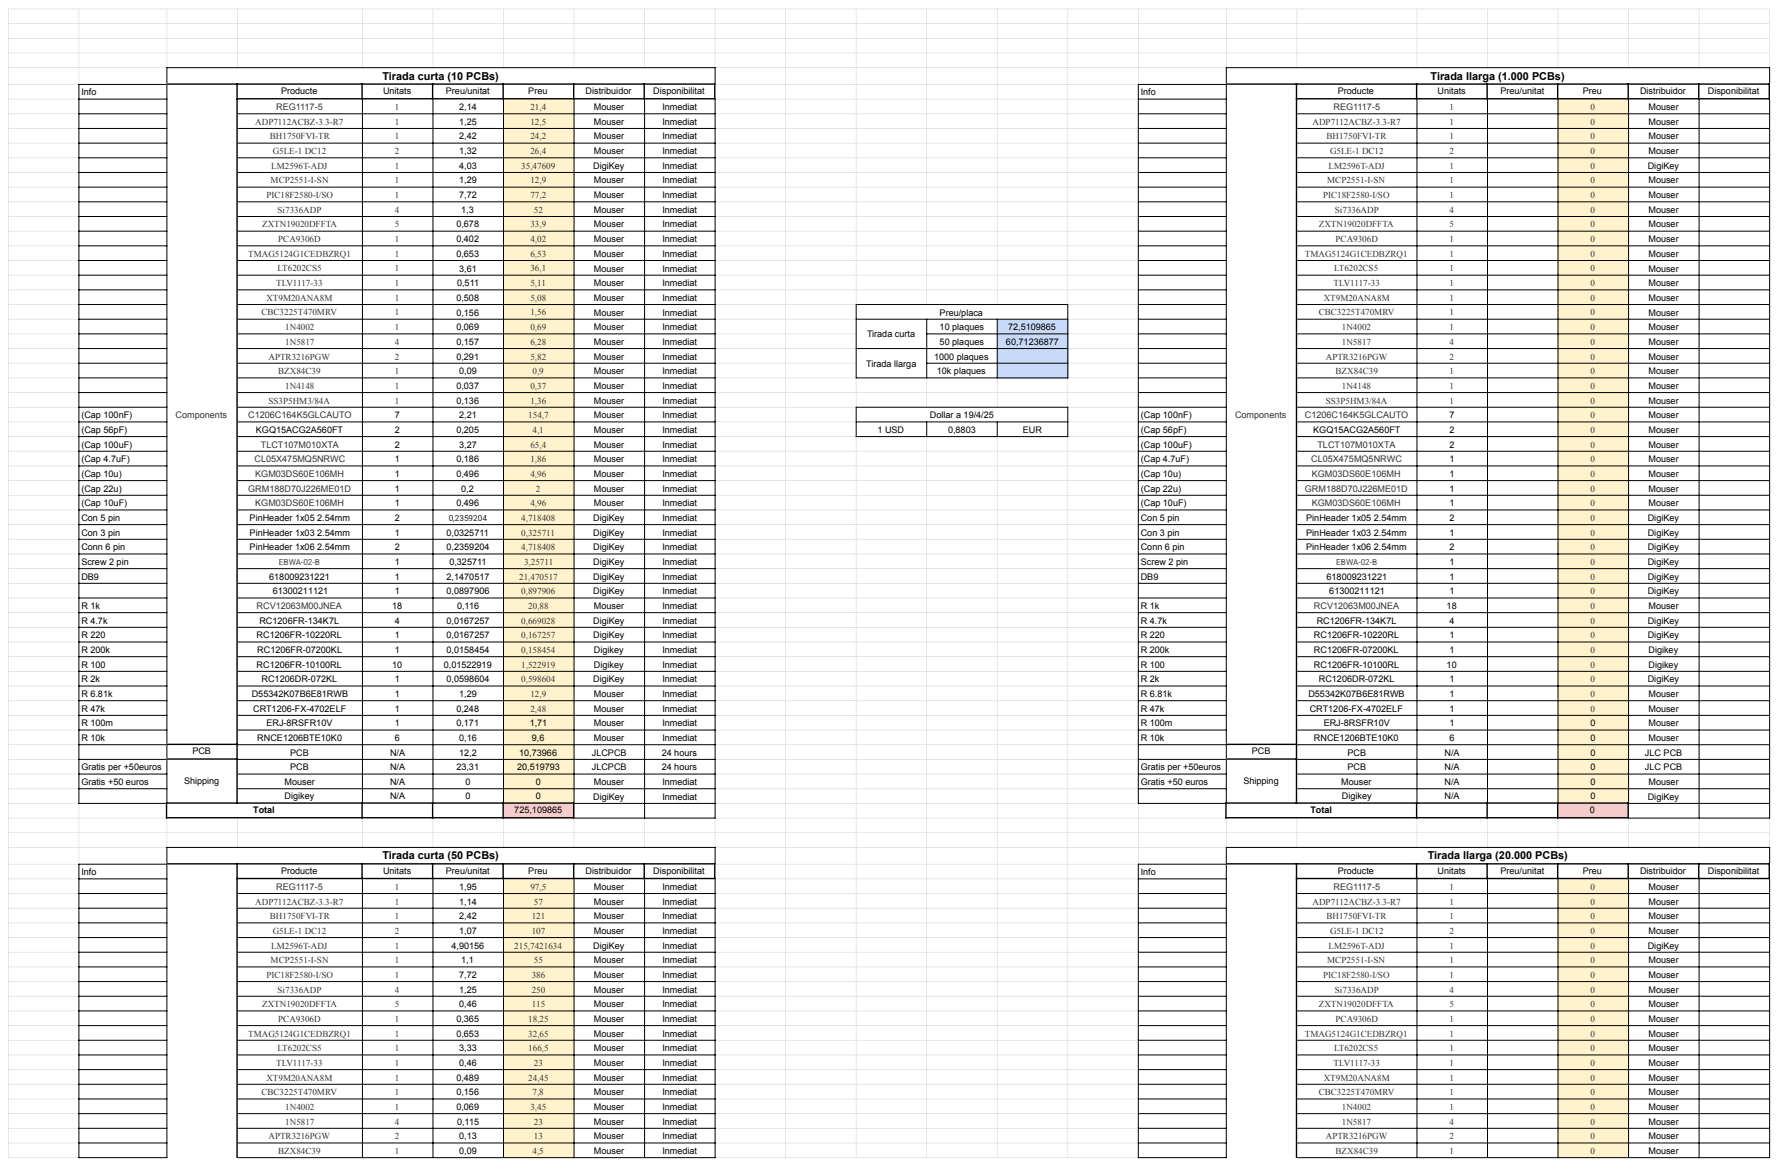
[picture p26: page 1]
Info; Components; Producte; Unitats; Preu/unitat; Preu; Distribuidor; Disponibilitat; Disponibilitat REG1117-5; Mouser; Inmediat; REG1117-5; Mouser ADP7112ACBZ-3.3-R7; ADP7112ACBZ-3.3-R7; Mouser BH1750FVI-TR; BH1750FVI-TR; Mouser G5LE-1 DC12; LM2596T-ADJ; DigiKey; DigiKey MCP2551-I-SN; MCP2551-I-SN; PIC18F2580-I/SO; Si7336ADP; ZXTN19020DFFTA; PCA9306D; TMAG5124G1CEDBZRQ1; TLV1117-33; Mouser XT9M20ANA8M; XT9M20ANA8M; Mouser CBC3225T470MRV; Preu/placa; CBC3225T470MRV; Tirada curta; 10 plaques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

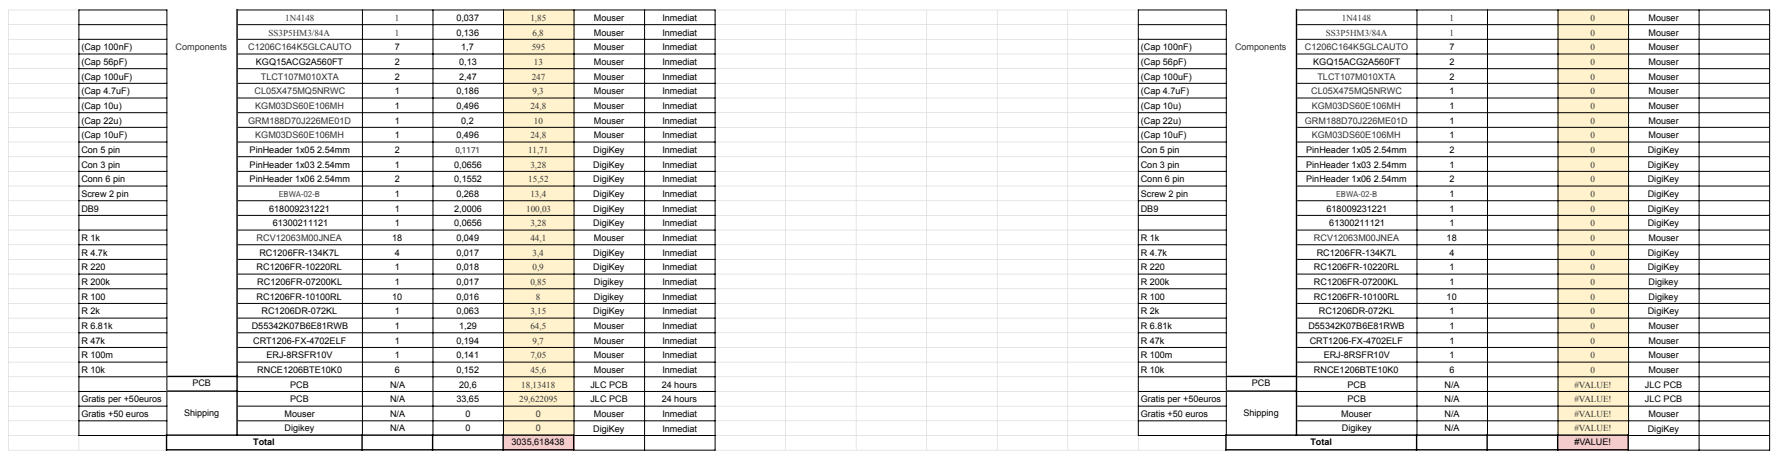
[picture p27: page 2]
Components; Mouser; Inmediat; (Cap 100nF); C1206C164K5GLCAUTO; (Cap 56pF); KGQ15ACG2A560FT; (Cap 100uF); TLCT107M010XTA; (Cap 4.7uF); CL05X475MQ5NRWC; (Cap 10u); KGM03DS60E106MH; (Cap 22u); GRM188D70J226ME01D; (Cap 10uF); Mouser Con 5 pin; PinHeader 1x05 2.54mm; DigiKey; Con 5 pin; DigiKey Con 3 pin; PinHeader 1x03 2.54mm; Con 3 pin; DigiKey Conn 6 pin; PinHeader 1x06 2.54mm; Conn 6 pin; DigiKey Screw 2 pin; EBWA-02-B; Screw 2 pin; DigiKey DB9; DigiKey R 1k; RCV12063M00JNEA; Mouser R 4.7k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

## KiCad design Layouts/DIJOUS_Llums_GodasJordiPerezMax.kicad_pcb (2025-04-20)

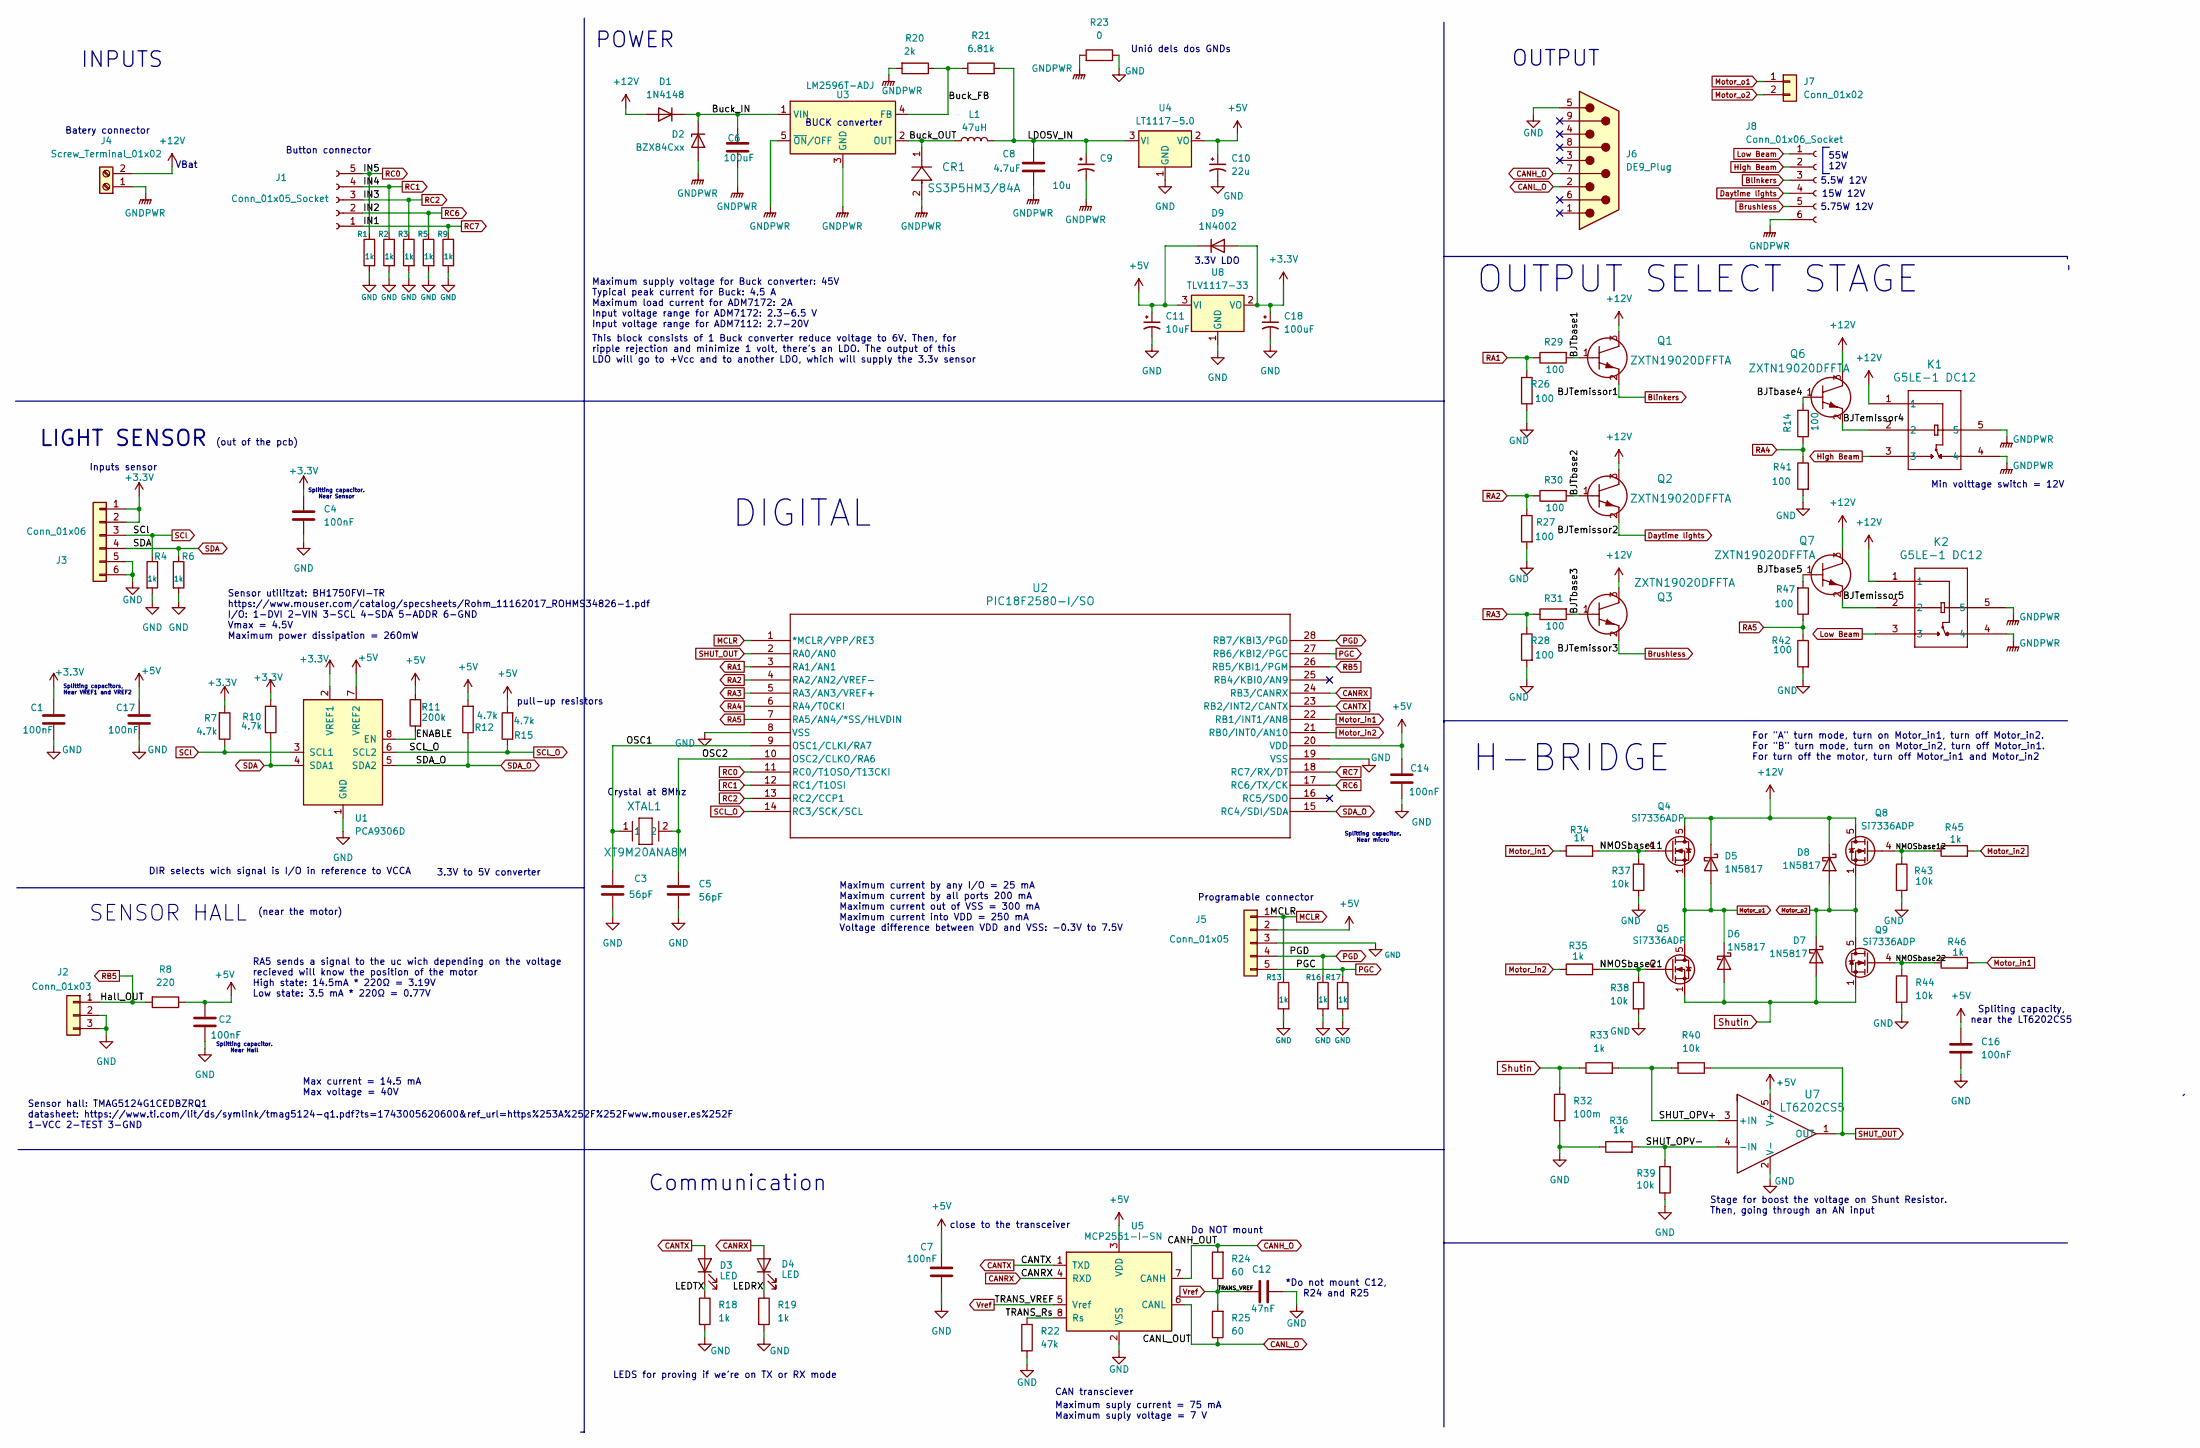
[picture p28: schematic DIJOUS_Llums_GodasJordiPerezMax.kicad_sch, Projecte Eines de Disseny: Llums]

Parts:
C1, C2, C4, C7, C14, C16, C17: 100nF; C_1206_3216Metric_Pad1.33x1.80mm_HandSolder
C3, C5: 56pF; C_0603_1608Metric
C6, C18: 100uF; C_1210_3225Metric
C8: 4.7uF; C_0402_1005Metric
C9: 10u; C_0201_0603Metric
C10: 22u; C_0402_1005Metric
C11: 10uF; C_0201_0603Metric
C12: 47nF
CR1: SS3P5HM3/84A; CR_5HM3&slash_84A_VIS
D1: 1N4148; D_DO-35_SOD27_P7.62mm_Horizontal
D2: BZX84Cxx; SOT-23
D3, D4: LED; LED_1206_3216Metric
D5, D6, D7, D8: 1N5817; D_DO-41_SOD81_P10.16mm_Horizontal
D9: 1N4002; D_DO-41_SOD81_P10.16mm_Horizontal
J1: Conn_01x05_Socket; PinHeader_1x05_P2.54mm_Vertical
J2: Conn_01x03; PinHeader_1x03_P2.54mm_Vertical
J3: Conn_01x06; PinHeader_1x06_P2.54mm_Vertical
J4: Screw_Terminal_01x02; TerminalBlock_Xinya_XY308-2.54-2P_1x02_P2.54mm_Horizontal
J5: Conn_01x05; PinHeader_1x05_P2.54mm_Vertical
J6: DE9_Plug; DSUB-9_Female_Horizontal_P2.77x2.54mm_EdgePinOffset9.40mm
J7: Conn_01x02; PinHeader_1x02_P2.54mm_Vertical
J8: Conn_01x06_Socket; PinHeader_1x06_P2.54mm_Vertical
K1, K2: G5LE-1 DC12; RELAY_G5LE-1 DC5_OMR
L1: 47uH; L_Neosid_Ms42
Q1, Q2, Q3, Q6, Q7: ZXTN19020DFFTA; ZXTN19020DFFTA_DIO
Q4, Q5, Q8, Q9: Si7336ADP; PowerPAK_SO-8_Single
R1, R2, R3, R4, R5, R6, R9, R13, R16, R17, R18, R19, R33, R34, R35, R36, R45, R46: 1k; R_1206_3216Metric
R7, R10, R12, R15: 4.7k; R_1206_3216Metric
R8: 220; R_1206_3216Metric
R11: 200k; C_0805_2012Metric
R14, R26, R27, R28, R29, R30, R31, R41, R42, R47: 100; R_1206_3216Metric
R20: 2k; R_1206_3216Metric
R21: 6.81k; R_1206_3216Metric
R22: 47k; R_1206_3216Metric
R23: 0; R_0805_2012Metric
R24, R25: 60
R32: 100m; R_0402_1005Metric
R37, R38, R39, R40, R43, R44: 10k; R_0402_1005Metric
U1: PCA9306D; SO-8_3.9x4.9mm_P1.27mm
U2: PIC18F2580-I/SO; SOIC-28W_7.5x17.9mm_P1.27mm
U3: LM2596T-ADJ; TO-220-5_P3.4x3.7mm_StaggerOdd_Lead3.8mm_Vertical
U4: LT1117-5.0; SOT-223-3_TabPin2
U5: MCP2551-I-SN; SOIC-8_3.9x4.9mm_P1.27mm
U7: LT6202CS5; S_5_ADI
U8: TLV1117-33; SOT-223
XTAL1: XT9M20ANA8M; XTAL_ANA8M_VIS

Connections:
+3.3V: C1.2, C4.1, C18.1, D9.2 (A), J3.1, J3.2, R7.2, R10.2, U1.2 (VREF1), U8.2 (VO)
+5V: C2.1, C7.1, C10.1, C11.1, C14.1, C16.1, C17.2, D9.1 (K), J5.2, R8.1, R11.1, R12.2, R15.2, U1.7 (VREF2), U2.20 (VDD), U4.2 (VO), U5.3 (VDD), U7.5 (V+), U8.3 (VI); also elsewhere on the board
+12V: D1.2 (A), D5.1 (K), D8.1 (K), J4.2, K1.1, K2.1, Q1.3, Q2.3, Q3.3, Q4.5 (D), Q6.3, Q7.3, Q8.5 (D)
/BJTbase1: Q1.1, R29.2
/BJTbase2: Q2.1, R30.2
/BJTbase3: Q3.1, R31.2
/BJTbase4: Q6.1, R14.2
/BJTbase5: Q7.1, R47.2
/BJTemissor4: K1.2, Q6.2
/BJTemissor5: K2.2, Q7.2
/Buck_FB: R20.1, R21.1, U3.4 (FB)
/Buck_IN: C6.1, D1.1 (K), D2.3 (K), U3.1 (VIN)
/Buck_OUT: CR1.1, L1.1, U3.2 (OUT)
/ENABLE: R11.2, U1.8 (EN)
/LDO5V_IN: C8.1, C9.1, L1.2, R21.2, U4.3 (VI)
/LEDRX: D4.1 (K), R19.1
/LEDTX: D3.1 (K), R18.1
/NMOSbase11: Q4.4 (G), R34.2, R37.1
/NMOSbase12: Q8.4 (G), R43.1, R45.1
/NMOSbase21: Q5.4 (G), R35.2, R38.1; also elsewhere on the board
/NMOSbase22: Q9.4 (G), R44.1, R46.1
/OSC1: C3.1, U2.9 (OSC1/CLKI/RA7), XTAL1.1
/OSC2: C5.1, U2.10 (OSC2/CLKO/RA6), XTAL1.2
/SHUT_OPV+: R33.2, R40.2, U7.3 (+IN)
/SHUT_OPV-: R36.2, R39.2, U7.4 (-IN)
/TRANS_Rs: R22.1, U5.8 (Rs)
Blinkers: J8.3, Q1.2
Brushless: J8.5, Q3.2
CANH_O: J6.7, R24.2, U5.7 (CANH)
CANL_O: J6.2, R25.1, U5.6 (CANL)
CANRX: D4.2 (A), U2.24 (RB3/CANRX), U5.4 (RXD)
CANTX: D3.2 (A), U2.23 (RB2/INT2/CANTX), U5.1 (TXD)
Daytime lights: J8.4, Q2.2
GND: C1.1, C2.2, C3.2, C4.2, C5.2, C7.2, C10.2, C11.2, C12.2, C14.2, C16.2, C17.1, C18.2, J2.2, J2.3, J3.5, J3.6, J5.3, J6.5, R1.2, R2.2, R3.2, R4.2, R5.2, R6.2, R9.2, R13.2, R16.2, R17.2, R18.2, R19.2, R22.2, R23.1, R26.2, R27.2, R28.2, R32.2, R36.1, R37.2, R38.2, R39.1, R41.2, R42.2, R43.2, R44.2, U1.1 (GND), U2.8 (VSS), U2.19 (VSS), U4.1 (GND), U5.2 (VSS), U7.2 (V-), U8.1 (GND); also elsewhere on the board
GNDPWR: C6.2, C8.2, C9.2, CR1.2, D2.1 (A), J4.1, J8.6, K1.4, K1.5, K2.4, K2.5, R20.2, R23.2, U3.3 (GND), U3.5 (~ON/OFF)
High Beam: J8.2, K1.3
Low Beam: J8.1, K2.3
MCLR: J5.1, R13.1, U2.1 (*MCLR/VPP/RE3)
Motor_in1: R34.1, R46.2, U2.22 (RB1/INT1/AN8)
Motor_in2: R35.1, R45.2, U2.21 (RB0/INT0/AN10)
Motor_o1: D5.2 (A), D6.1 (K), J7.1, Q4.1 (S), Q4.2 (S), Q4.3 (S), Q5.5 (D)
Motor_o2: D7.1 (K), D8.2 (A), J7.2, Q8.1 (S), Q8.2 (S), Q8.3 (S), Q9.5 (D)
PGC: J5.5, R17.1, U2.27 (RB6/KBI2/PGC)
PGD: J5.4, R16.1, U2.28 (RB7/KBI3/PGD)
RA1: R26.1, R29.1, U2.3 (RA1/AN1)
RA2: R27.1, R30.1, U2.4 (RA2/AN2/VREF-)
RA3: R28.1, R31.1, U2.5 (RA3/AN3/VREF+)
RA4: R14.1, R41.1, U2.6 (RA4/T0CKI)
RA5: R42.1, R47.1, U2.7 (RA5/AN4/*SS/HLVDIN)
RB5: J2.1, R8.2, U2.26 (RB5/KBI1/PGM)
RC0: J1.5, R1.1, U2.11 (RC0/T1OSO/T13CKI)
RC1: J1.4, R2.1, U2.12 (RC1/T1OSI)
RC2: J1.3, R3.1, U2.13 (RC2/CCP1)
RC6: J1.2, R5.1, U2.17 (RC6/TX/CK)
RC7: J1.1, R9.1, U2.18 (RC7/RX/DT)
SCL_O: R15.1, U1.6 (SCL2), U2.14 (RC3/SCK/SCL)
SCl: J3.3, R4.1, R7.1, U1.3 (SCL1)
SDA: J3.4, R6.1, R10.1, U1.4 (SDA1)
SDA_O: R12.1, U1.5 (SDA2), U2.15 (RC4/SDI/SDA)
SHUT_OUT: R40.1, U2.2 (RA0/AN0), U7.1 (OUT)
Shutin: D6.2 (A), D7.2 (A), Q5.1 (S), Q5.2 (S), Q5.3 (S), Q9.1 (S), Q9.2 (S), Q9.3 (S), R32.1, R33.1
Vref: C12.1, R24.1, R25.2, U5.5 (Vref)

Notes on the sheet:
Max current = 14.5 mA Max voltage = 40V
5.75W 12V
INPUTS
Batery connector
(out of the pcb)
Unió dels dos GNDs
SENSOR HALL
DIR selects wich signal is I/O in reference to VCCA
close to the transceiver
Maximum supply voltage for Buck converter: 45V Typical peak current for Buck: 4.5 A Maximum load current for ADM7172: 2A Input voltage range for ADM7172: 2.3-6.5 V Input voltage range for ADM7112: 2.7-20V
Splitting capacitor. Near Hall
Splitting capacitors, Near VREF1 and VREF2
Splitting capacitor. Near Sensor
Spliting capacity, near the LT6202CS5
OUTPUT SELECT STAGE
*Do not mount C12, R24 and R25
Do NOT mount
H-BRIDGE
pull-up resistors
LEDS for proving if we're on TX or RX mode
POWER
Communication
Maximum current by any I/O = 25 mA Maximum current by all ports 200 mA Maximum current out of VSS = 300 mA Maximum current into VDD = 250 mA Voltage difference between VDD and VSS: -0.3V to 7.5V
Sensor utilitzat: BH1750FVI-TR https://www.mouser.com/catalog/specsheets/Rohm_11162017_ROHMS34826-1.pdf I/O: 1-DVI 2-VIN 3-SCL 4-SDA 5-ADDR 6-GND Vmax = 4.5V Maximum power dissipation = 260mW
LIGHT SENSOR
5.5W 12V
This block consists of 1 Buck converter reduce voltage to 6V. Then, for ripple rejection and minimize 1 volt, there's an LDO. The output of this LDO will go to +Vcc and to another LDO, which will supply the 3.3v sensor
Inputs sensor
3.3V to 5V converter
BUCK converter
Button connector
Stage for boost the voltage on Shunt Resistor. Then, going through an AN input
OUTPUT
RA5 sends a signal to the uc wich depending on the voltage recieved will know the position of the motor High state: 14.5mA * 220Ω = 3.19V Low state: 3.5 mA * 220Ω = 0.77V
(near the motor)
Min volttage switch = 12V
Maximum suply current = 75 mA Maximum suply voltage = 7 V
CAN transciever
VBat
15W 12V

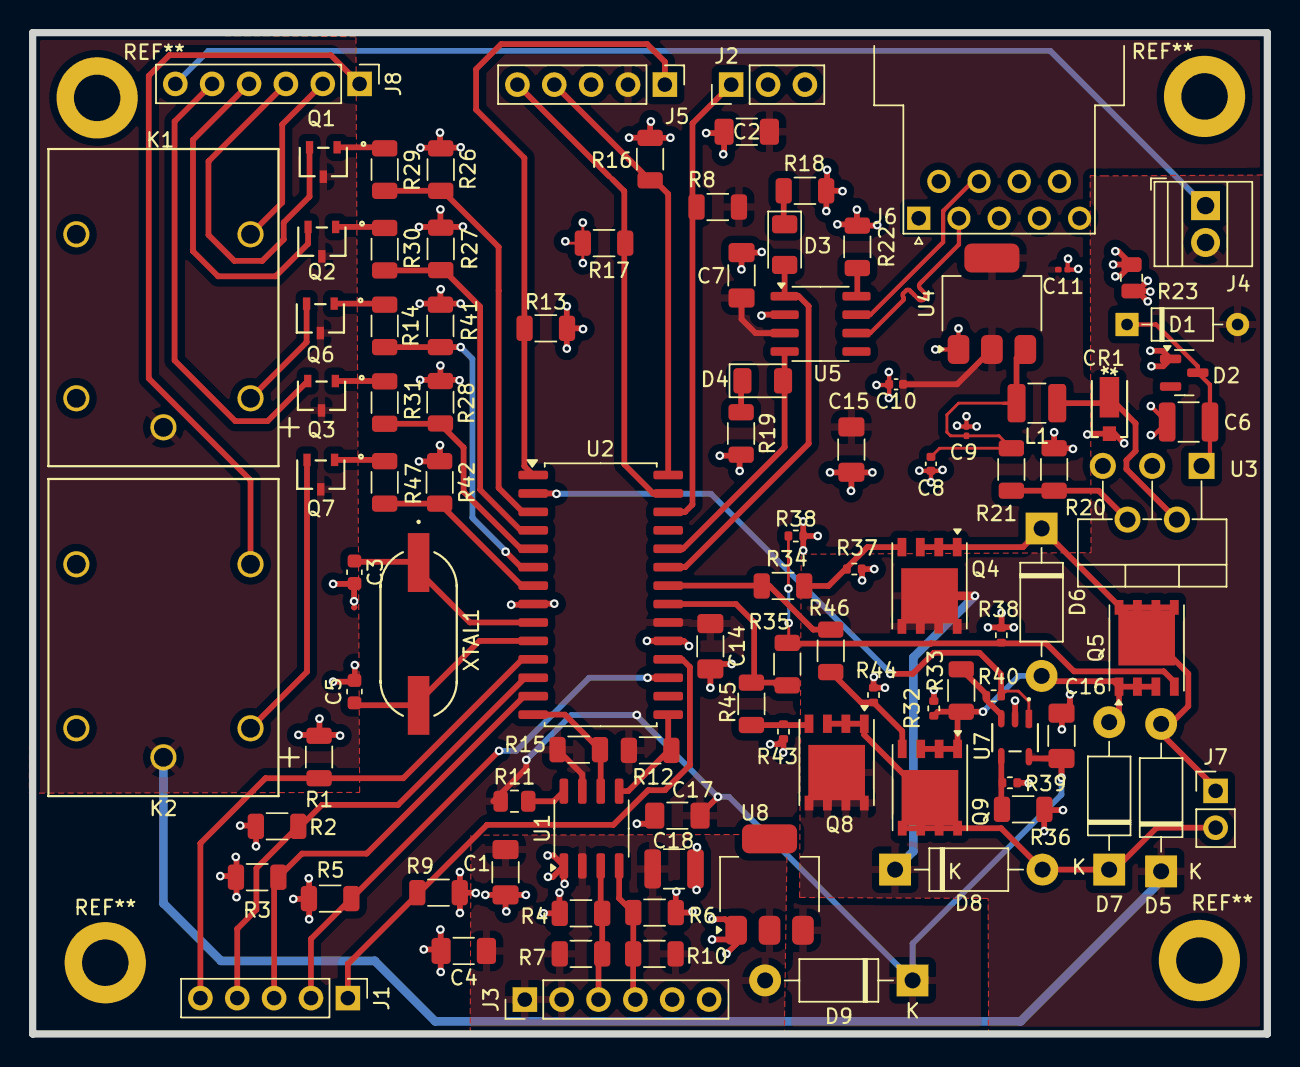
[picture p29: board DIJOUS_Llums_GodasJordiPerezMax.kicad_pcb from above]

Board: 2 copper layers, 85.1 x 69.0 mm, 100 parts (0 on the bottom side), 61 nets.

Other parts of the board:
C15: 4.7uF; C_1206_3216Metric_Pad1.33x1.80mm_HandSolder
R38#2: 10k; R_0402_1005Metric

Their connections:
+5V: C15.1; also elsewhere on the board
/NMOSbase21: R38#2.1; also elsewhere on the board
GND: C15.2, R38#2.2; also elsewhere on the board

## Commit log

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2025-03-23 3rd revision of the schematic
    [DIJOUS_Llums_GodasJordiPerezMax.kicad_pcb, DIJOUS_Llums_GodasJordiPerezMax.kicad_sch]
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2025-03-24 LTSpice Power Stage
    Etapa de Power simulada. Si no hay problemas con el CAD de estos modelos, es definitiva. Consta de un Buck y 2 LDO
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2025-03-25 Update DIJOUS_Llums_GodasJordiPerezMax
    Update v4 by Jordi
    [DIJOUS_Llums_GodasJordiPerezMax (1).kicad_sch]
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2025-03-25 Update and rename DIJOUS_Llums_GodasJordiPerezMax.kicad_sch to Schematics/DIJOUS_Llums_GodasJordiPerezMax.kicad_sch
    [DIJOUS_Llums_GodasJordiPerezMax.kicad_sch]
2025-03-25 Update and rename DIJOUS_Llums_GodasJordiPerezMax_v3/DIJOUS_Llums_GodasJordiPerezMax.kicad_sch to DIJOUS_Llums_GodasJordiPerezMax_v3/Schematics/DIJOUS_Llums_GodasJordiPerezMax.kicad_sch
    [DIJOUS_Llums_GodasJordiPerezMax.kicad_sch]
2025-03-25 Update and rename DIJOUS_Llums_GodasJordiPerezMax_v4/DIJOUS_Llums_GodasJordiPerezMax.kicad_sch to DIJOUS_Llums_GodasJordiPerezMax_v4/Schematics/DIJOUS_Llums_GodasJordiPerezMax.kicad_sch
    [DIJOUS_Llums_GodasJordiPerezMax.kicad_sch]
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2025-03-25 Rename DIJOUS_Llums_GodasJordiPerezMax_v4/DIJOUS_Llums_GodasJordiPerezMax.kicad_pcb to DIJOUS_Llums_GodasJordiPerezMax_v4/Layouts/DIJOUS_Llums_GodasJordiPerezMax.kicad_pcb
    Layout
    [DIJOUS_Llums_GodasJordiPerezMax.kicad_pcb]
2025-03-25 Rename DIJOUS_Llums_GodasJordiPerezMax_v3/DIJOUS_Llums_GodasJordiPerezMax.kicad_pcb to DIJOUS_Llums_GodasJordiPerezMax_v3/Layouts/DIJOUS_Llums_GodasJordiPerezMax.kicad_pcb
    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
    [DIJOUS_Llums_GodasJordiPerezMax.kicad_pcb]
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2025-03-25 Rename DIJOUS_Llums_GodasJordiPerezMax_v3/Layouts/DIJOUS_Llums_GodasJordiPerezMax.kicad_pcb to Layouts/DIJOUS_Llums_GodasJordiPerezMax_v3DIJOUS_Llums_GodasJordiPerezMax.kicad_pcb
    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
    [DIJOUS_Llums_GodasJordiPerezMax_v3DIJOUS_Llums_GodasJordiPerezMax.kicad_pcb]
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2025-03-25 Update and rename DIJOUS_Llums_GodasJordiPerezMax_v3/Schematics/DIJOUS_Llums_GodasJordiPerezMax.kicad_sch to Schematics/DIJOUS_Llums_GodasJordiPerezMax_v3DIJOUS_Llums_GodasJordiPerezMax.kicad_sch
    Esquemático
    [DIJOUS_Llums_GodasJordiPerezMax_v3DIJOUS_Llums_GodasJordiPerezMax.kicad_sch]
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2025-03-25 Rename DIJOUS_Llums_GodasJordiPerezMax_v4/Layouts/DIJOUS_Llums_GodasJordiPerezMax.kicad_pcb to Layouts/DIJOUS_Llums_GodasJordiPerezMax_v4DIJOUS_Llums_GodasJordiPerezMax.kicad_pcb
    Layouts
    [DIJOUS_Llums_GodasJordiPerezMax_v4DIJOUS_Llums_GodasJordiPerezMax.kicad_pcb]
2025-03-25 Update and rename DIJOUS_Llums_GodasJordiPerezMax_v4/Schematics/DIJOUS_Llums_GodasJordiPerezMax.kicad_sch to Schematics/DIJOUS_Llums_GodasJordiPerezMax_v4DIJOUS_Llums_GodasJordiPerezMax.kicad_sch
    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
    [DIJOUS_Llums_GodasJordiPerezMax_v4DIJOUS_Llums_GodasJordiPerezMax.kicad_sch]
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2025-03-25 Input and Power stage simulation
    Simulación de etapa Input y Power. Consta de la etapa Safe Input (díodos protección) + Buck converter y 2 LDO. Funciona correctamente
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2025-03-26 shcematic v6- versio per presentar
    [DIJOUS_Llums_GodasJordiPerezMax_v6.kicad_sch]
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2025-03-29 Update DIJOUS_Llums_GodasJordiPerezMax.kicad_sch
    Resistencias botones y update puente + shunt y alguna footprint
    [DIJOUS_Llums_GodasJordiPerezMax.kicad_sch]
2025-03-29 Update DIJOUS_Llums_GodasJordiPerezMax.kicad_sch
    Nueva actualización Puente H+ resistencia Shunt. Se han añadido bastantes huellas. Falta huellas restantes y la etapa Output select y se puede empezar Placement
    [DIJOUS_Llums_GodasJordiPerezMax.kicad_sch]
2025-03-30 Update DIJOUS_Llums_GodasJordiPerezMax.kicad_sch
    Alguna pequeña corrección del esquemático. He añadido un par de huellas y cambiado algún pin que estaba mal. Faltan aún huellas por poner y alguna etapa por revisar (la del Hall y el Output select st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
    [DIJOUS_Llums_GodasJordiPerezMax.kicad_sch]
2025-03-30 Update DIJOUS_Llums_GodasJordiPerezMax.kicad_pcb
    Primer Placement del proyecto. He hecho placement de los inputs, el buck converter y su etapa de filtrado, el puente H, el DB-9, la etapa de comunicaciones y del intranivel. Faltan algunas footprints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
    [DIJOUS_Llums_GodasJordiPerezMax.kicad_pcb]
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2025-03-31 Update DIJOUS_Llums_GodasJordiPerezMax.kicad_pcb
    Primer avance en PCB. Se ha hecho Placement de una parte de los componentes, separación de planos de masa y potencia y el routing del Buck, del puente H, algunas conexiones del micro e inputs y outpu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
    [DIJOUS_Llums_GodasJordiPerezMax.kicad_pcb]
2025-04-02 Update esquemático
    Versión 2.0 del esquemático. Cambios notables respecto a la semana pasada
    [DIJOUS_Llums_GodasJordiPerezMax.kicad_sch]
2025-04-02 Update Layout
    Versión 1.0 del Layout. En este Commit, se han ruteado algunos GND de SMD y mejorado la interconexión en algunos puntos concretos. A falta del okey del otro compañero
    [DIJOUS_Llums_GodasJordiPerezMax.kicad_pcb]
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2025-04-12 Update esquemàtic
    S'ha modificat el LDO de 6 a 5V i alguns footprints que no estaven ben assignats
    [DIJOUS_Llums_GodasJordiPerezMax.kicad_sch]
2025-04-12 Update PCB
    S'ha reorganitzat la zona de potència gràcies a un forat que ha deixat el DB-9. S'han col·locat les noves footprints canviades
    [DIJOUS_Llums_GodasJordiPerezMax.kicad_pcb]
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
